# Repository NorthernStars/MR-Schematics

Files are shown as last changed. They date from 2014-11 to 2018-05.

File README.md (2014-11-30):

MR-Schematics
============

This repository includes schematic and pcb layout files for some electronical hardware of the Mixed-Reality system.
Cadsoft Eagle (http://www.cadsoftusa.com/?lang=en) is used to generate the these files. Sometimes also a partlist is included.

Included Files
-----
This repository includes files for the following hardware:
* mrShark - Robot mrShark including programmer and debug/charger boards
* IR Testboard - Board for redirecting serial and IR data for debugging
* IR Transmitter - USB Infrared transmitter
* IR Splitter - Splitter for IR system with high current
* LiPo-Charger MultiBoard - Small Robot LiPo chargers that are connectable to any size of charger station
* LiPo-Charger-Station - 3x3 Robot LiPo charger station with microcontroller

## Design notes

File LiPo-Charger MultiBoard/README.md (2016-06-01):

LiPo-Charger MultiBoard
=======================
This charger consists of several small 50x50mm board that can get connected to each other to build a charger station of your preferred size.
* The charger board includes charging circuits for charging two LiPo batteries with ~200mA/battery.
* The supply board is for connecting the charger boards to a 5V power suplly. Maximum output current ist 5.0A. It's recommended to use max. 10 charger boards at one supply board.

Order online
------------
The pcbs can be ordered very cheap from www.dirtypcbs.com
* Charger: http://dirtypcbs.com/view.php?share=21687&accesskey=b3ce18c981010ed7b3aafff49d6ba531
* Supply: http://dirtypcbs.com/view.php?share=3158&accesskey=d8e7d692d385bc674d54f8e41f2b1a86

The electronic parts should get ordered from Farnell (http://www.farnell.com) and Reichelt (https://secure.reichelt.de/index.html?LANGUAGE=EN).

The LibreOffice calculation Parts-Calculation.ods includes an adjustable list of parts to oder.

Usage
-----
To use the charger, connect at least one charger board to the supply board.
Connect the supply board with your 5V power supply. Attention: There is no protection circuit for higher voltages!
You can connect other chargers to the other sides of any charger already connected to the supply board or to the supply board itself.

I²C / TWI Bus
-------
The charger boards include a I²C (or TWI) interface to connect a microcontroller or any other logic to the robots.
For that the charger board stops the robot (depending on the correct firmware) from booting. After that you can access the robot internal hardware via I²C bus.

There will be an additional board to manage the robots in the future.

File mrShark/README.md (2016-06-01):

mrShark
=======
Here you find schemtics and board layout needed for the Mixed-Relality Robot mrShark.
The main board is the mrShark controlling everything on the robot.
For programming you also need the programmer board. Optional you can use the debuger board to charge the robots batteries and use the serial debug interface to test the robot without infrared communication.

## What you need

* mrShark (main controller board, always use latest version)
* LED-Marker (vision detection marker) 
* mrShark Adapter (programming, debugging and charging)

Also consider using the LiPo-Charger-Multiboard for charging larger sets of robots.

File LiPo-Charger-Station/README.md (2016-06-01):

LiPo-Charger-Station
====================

## DO NOT USE, NOT TESTED AND LAYOUT OUTDATED

This charger station includes LiPo charger circuits to charge 9 robots with 2 LiPo batterys each.
Each battery will be charged with ~500mA. The station includes a microcontroller to access the robots internal hardware.

This project currently not maintained and includes some erros. Use LiPo-Charger MutliBoard instead.

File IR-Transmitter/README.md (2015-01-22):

IR-Transmitter
==============
Use this infrared transmitter to send commands data to the Mixed-Reality robots.
The boeard has a USB connector with and FTDI USB-to-Serial converter so you can plug this board directly into you computer.
The board uses a 115.2kbit/s transmission rate for sending infrared data.

Add a power supply to V+ and GND. You can add any power supply from 5V to 12V (7.5V is recommended).
Add some infrared leds to the LED+ and LED- pads.

You can use the jumper JP1 to use the USB 5V bus power to get a portable IR-Transmitter.
Take care that the maximum output current of the USB bus is 500mA.
If you add ~4 IR-LEDs it should work.

For small mobile IR-Transmitter select a suitable resistor for R2 and don't assemble R3.

Be aware that this board isn't build for high currents!
For that use the IR-Splitter. Maybe you also should use a heatsink on the MOSFET.
To do so, bridge resistor R2 and use 1k ohm resistor for R3. Connect IR data signal for IR-Splitter to LED- and GND of IR-Splitter to GND.

Order
-----
You can order this transmitter via www.dirtypcbs.com
* http://dirtypcbs.com/view.php?share=3876&accesskey=a4be5c8c025c9f4713186b7ca5dc06cf

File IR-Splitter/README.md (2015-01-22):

IR-Splitter
===========
Hardware to split IR data load to seperate MOSFET channels.
Connect external power supply and IR data from IR-Transmitter to the board.
Voltage of power supply depends on you needs but test show that it should be between 5V and 12V (7.5V is recommended).

Connect IR-leds to the 10 IR-OUT pads. Try to balance the number of leds on the channels.
It's highly recommended to use a heatsink on the mosfets.

Test your installation with different intervals of load.
MOSFET's temperature should not be above 80°C!

It is possible to use this pcb as single layer board.

ATTENTION
---------
If you don't use our IR-Transmitter, take care that the IR-Splitter needs an inverted IR data input signal. So HIGH level is LOW and the other way round.

Also be aware that setting IR data input signal to LOW level will cause the leds to light up. This maybe damages them!

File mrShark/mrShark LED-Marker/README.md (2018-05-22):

# mrShark LED-Marker
LEd marker for Mixed-Reality Robotr mrShark.
Includes 3x3 led arry an 4 position lights.
Controlled via I2C/TWI PC9552 led controller.

## PCB Order
Order on 

https://jlcpcb.com/

and upload Gerber File zip.
Dimension of pcb is 26mm x 32mm
    
## Assembly
Place LEDs, ICs and R1, R2, R3 as shown in schematics.
Choose R4 - R11 and R21 corresponding to your LED current (volatge of mrShark is max. 4.1V, average 3.0 - 3.3V, min 2.7V).
Choose R12, R13 for two! LEDs.

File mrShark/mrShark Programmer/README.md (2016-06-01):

# mrShark Programmer
Programming adapter using In-System,-Programming (ISP) over SPI bus of controller.

## DO NOT USE ANYMORE, LAYOUT OUTDATED

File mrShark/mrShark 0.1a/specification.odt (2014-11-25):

mrShark

Platinen-Datenblatt

Platinen-Daten:

Abmaße: | 27x25mm
Bohrungen: | 4x1,5mm (Durchmesser) Vias: 0,24mm
Datenformat: | Eagle (Schaltplan, Platinenlayout) + Datenblatt
Materialdaten: | 35µmCu 1,0mm
Fertigungsdaten: | Lötstopplack (beidseitig) min. Leiterbahnabstand = 6mil (0,150mm)

Bestückung:

Anzahl | Bauteil [Gehäusetyp] | Wert
2 | Kondensator [402] | 18pF
1 | Kondensator [402] | 100nF
2 | Widerstand [0402] | 1kΩ
1 | Buchse 12 Kontakte, RM=0,5mm | Hirose - DF23C-12DS-0.5V(92)
1 | Buchsenleiste 4 Kontakte, RM=2,54mm
2 | Diode [SOT36] | NXP - BAS70-07S
1 | Mikrocontroller [QFN] | Atmel AVR - ATtiny 4313-MU
1 | Motortreiber [10-DFN/MLP] | Allegro Microsystems - A3901SEJTR-T
1 | IRDA-Controller [SOIC] | Microchip - MCP2120-I/SL
1 | IRDA-transciever | Vishay - TFBS4711-TR1
4 | RGB-LED [PLCC6] | Avago Technologies - ASMT-YTD2-0BB02
1 | LED green[0603] | Kingbright - KPT-1608SGC
1 | Quarz 14,7456MHz [CFPX-104] | IQD frequency products - CFPX-104 50/50/10/18 14.7456MHZ
1 | Schalter 2-Polig [DIL] | Multicomp - MCEMR-02-T
2 | Dual NPN Transistor [SOT363] | Rohm - UMX3NTR

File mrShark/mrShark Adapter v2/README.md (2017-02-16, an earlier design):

# mrShark Adapter v2
Additional version of the mrShark Adapter that can be soldered by humans.

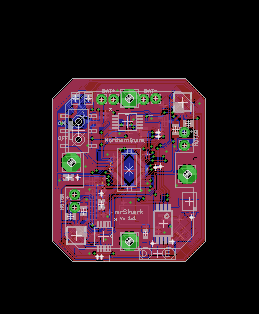
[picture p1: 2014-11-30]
mrShark/mrShark 1.2/board.png

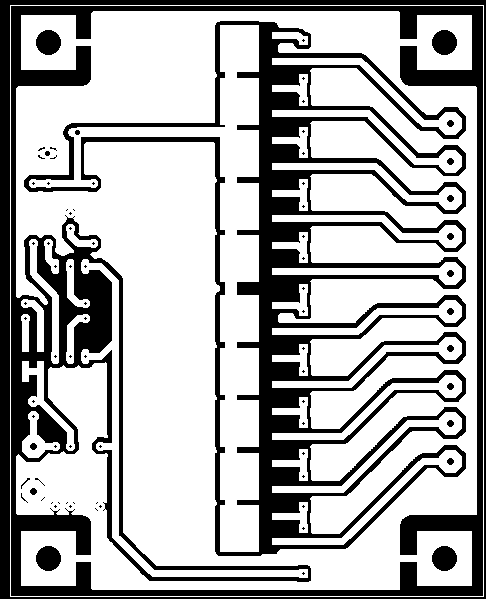
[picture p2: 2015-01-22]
IR-Splitter/layout.png

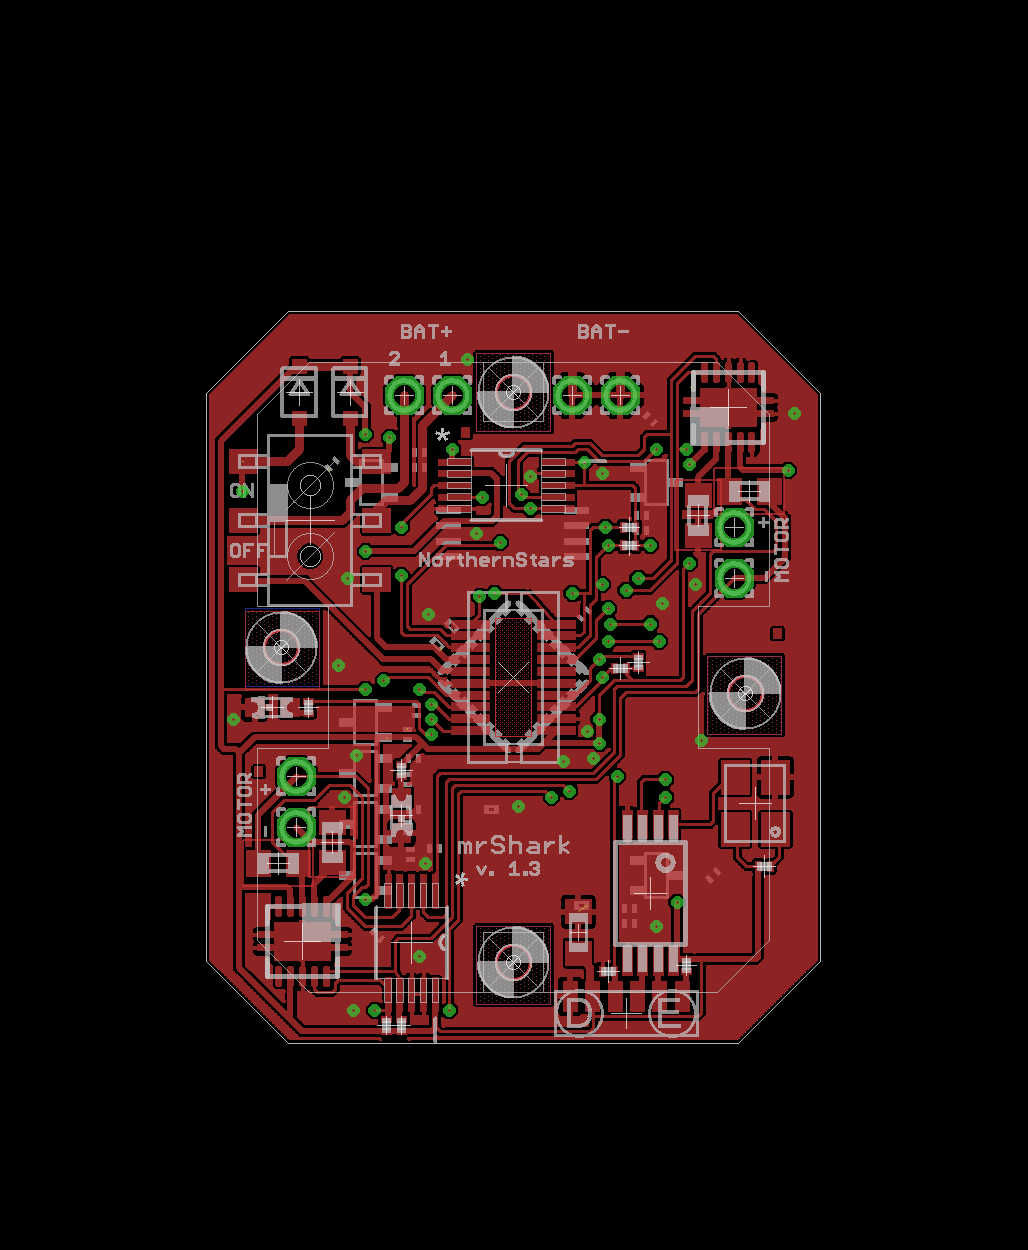
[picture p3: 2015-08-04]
mrShark/mrShark 1.4/TOP-Layer.png

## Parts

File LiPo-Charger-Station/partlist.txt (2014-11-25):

Partname,Value,Package
C1,100n,C0201
C2,100n,C0201
CON_PROG,2X8C7852,7852-2X8
IC1,ATMEGA48/88/168-MU,MLF32
IC2,PCA9306DC,VSSOP8
IC3,TIR1000PWR,PW_R-PDSO-G08
IC4,TFBS4711TR1,TFBS4711
IC5,DRV8830DGQRWSON,S-PDSO-N10
IC6,LTC2990IMSPBF,SOP50P490X110-10N
IC7,DRV8830DGQRWSON,S-PDSO-N10
IC8,LTC2990IMSPBF,SOP50P490X110-10N
LED1,green,CHIPLED_0603
LED2,ASMT-YTD2-0BB02,PLCC6K
LED3,ASMT-YTD2-0BB02,PLCC6K
LED4,ASMT-YTD2-0BB02,PLCC6K
LED5,ASMT-YTD2-0BB02,PLCC6K
LED6,red,CHIPLED_0603
Q1,ASFLM1-1.8432MHZ-L-C-T,HC536
Q2,BC817W,SOT323-BEC
Q3,BC817W,SOT323-BEC
Q4,BC817W,SOT323-BEC
Q5,BC817W,SOT323-BEC
Q6,BC817W,SOT323-BEC
Q7,BC817W,SOT323-BEC
Q8,BC817W,SOT323-BEC
R1,100k,R0201
R2,100k,R0201
R3,100k,R0201
R4,100k,R0201
R5,100k,R0201
R6,130R,R0201
R7,1k8,R0201
R8,1k8,R0201
R9,100k,R0201
R10,27R,R0201
R11,2k,R0201
R12,1k,R0201
R13,2k,R0201
R14,100k,R0201
R15,100k,R0201
R16,100k,R0201
R17,100k,R0201
R18,100k,R0201
R19,560R,R0201
R20,560R,R0201
R21,130R,R0201
R22,130R,R0201
R23,100k,R0201
R24,100k,R0201
R25,560R,R0201
R26,560R,R0201
R27,130R,R0201
R28,130R,R0201
R29,0.95R,R0201
R30,0R2,R0201
R31,0.95R,R0201
R32,0R2,R0201
R33,130R,R0201
R34,1k8,R0201
R35,1k8,R0201
SWITCH_PWR,AYZ0202AGRLC,AYZ0202AGLRC

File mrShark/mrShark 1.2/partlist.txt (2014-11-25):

------------------------------------------------
Eagle partlist from mrshark 11.sch at 24.11.2014 14:29:40
------------------------------------------------

------------------------
PLCC6K
	PLCC6K
		4x	ASMT-YTD2-0BB02
			['LED2', 'LED3', 'LED4', 'LED5']

------------------------
C-EUC0201
	C0201
		2x	18p
			['C3', 'C4']

------------------------
C-EUC0603K
	C0603K
		1x	10µ
			['C5']

------------------------
AYZ0202AGRLC
	AYZ0202AGLRC
		1x	AYZ0202AGRLC
			['SWITCH_PWR']

------------------------
ATMEGA48/88/168-MU
	MLF32
		1x	ATMEGA168-20MU
			['IC1']

------------------------
R-EU_R0201
	R0201
		2x	1k8
			['R34', 'R35']

------------------------
-
	7X-1.8432MBB-T
		1x	TXC
			['Q1']

------------------------
DF12-20DP
	DF12-20DP
		1x	DF12(5.0)-20DP-0.5V
			['CON_PROG']

------------------------
MOUNT-PAD-SQUARE1,5
	0,75-PAD-SQUARE
		4x	MOUNT-PAD-SQUARE1,5
			['H1', 'H2', 'H3', 'H4']

------------------------
R-EU_R0603
	R0603
		1x	0R2
			['R32']

------------------------
BC817W
	SOT323-BEC
		7x	BC817W
			['Q2', 'Q3', 'Q4', 'Q5', 'Q6', 'Q7', 'Q8']

------------------------
DRV8830DGQRWSON
	S-PDSO-N10
		2x	DRV8830DRCT
			['IC5', 'IC7']

------------------------
PCA9540TSSOP8
	TSSOP8
		1x	PCA9540BDP
			['IC2']

------------------------
TXC-7B-SERIESSMD
	TXC_7B_SERIES
		1x	14,7456MHZ
			['Q9']

------------------------
1,6/0,9
	wirepad
		8x	1,6/0,9
			['BAT1+1', 'BAT1-1', 'BAT2+1', 'BAT2-1', 'MOT1', 'MOT2', 'MOT3', 'MOT4']

------------------------
LTC2990IMSPBF
	SOP50P490X110-10N
		2x	LTC2990IMS#PBF
			['IC6', 'IC8']

------------------------
TFBS4711TR1
	TFBS4711
		1x	TFBS4711TR1
			['IC4']

------------------------
PMEG2010EAR
	SOD323-R
		2x	PMEG2010EA
			['D1', 'D2']

------------------------
TIR1000PWR
	PW_R-PDSO-G08
		1x	TIR1000PWR
			['IC3']

------------------------
LEDCHIPLED_0603
	CHIPLED_0603
		1x	red
			['LED6']

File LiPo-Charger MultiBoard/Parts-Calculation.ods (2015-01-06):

LiPo-Charger MultiBoard
Parts calculation
Last Update: | 2014/11/26
No. of Charger Boards: | 20
No. of Supply Boards: | 10
Part | Type | Quantity | # ordered | Farnell Order No. | Price | Total | Toal ordered | Quantity | # ordered | Reichelt Order No. | Price | Total | Total ordered
Pinheader Male | 2.54“ RM, THT | 150 | 150 | 1593428 | 0,054 € | 8,12 € | 8,12 € | 15 | 0 | SL 1X40W 2,54 | 0,300 € | 4,500 € | 0,00 €
Pinheader Female | 2,54“ RM, THT | 150 | 0 | 1804766 | 0,437 € | 65,55 € | 0,00 € | 30 | 30 | BL 1X20W8 2,54 | 0,460 € | 13,800 € | 13,80 €
Resistor 5k6 | SMD 1206 | 50 | 50 | 9236864 | 0,009 € | 0,47 € | 0,47 € | 40 | 0 | SMD 1/4W 5,6K | 0,082 € | 3,280 € | 0,00 €
Resistor 1k8 | SMD 1206 | 100 | 100 | 2139458 | 0,010 € | 1,00 € | 1,00 € | 60 | 0 | SMD 1/4W 1,8K | 0,082 € | 4,920 € | 0,00 €
Resistor 470R | SMD 1206 | 50 | 50 | 9240489 | 0,017 € | 0,85 € | 0,85 € | 50 | 0 | SMD 1/4W 470 | 0,082 € | 4,100 € | 0,00 €
LED red | SMD 1206 | 40 | 40 | 2099245 | 0,078 € | 3,12 € | 3,12 € | 40 | 0 | SMD-LED 1206 RT | 0,110 € | 4,400 € | 0,00 €
LED green | SMD 1206 | 10 | 10 | 2099247 | 0,069 € | 0,69 € | 0,69 € | 10 | 0 | SMD-LED 1206 GN | 0,100 € | 1,000 € | 0,00 €
MCP73832T | SOT-23 | 40 | 40 | 1834891 | 0,363 € | 14,52 € | 14,52 € | 40 | 0 |  |  | 0,000 € | 0,00 €
Header DF12-20DS |  | 20 | 20 | 1324621 | 0,697 € | 13,94 € | 13,94 € | 20 | 0 |  |  | 0,000 € | 0,00 €
Connector Wago 250-202 |  | 10 | 0 | 1891580 | 0,460 € | 4,60 € | 0,00 € | 10 | 10 | WAGO 250-202 | 0,450 € | 4,500 € | 4,50 €
AP1084D33 | TO-252 | 10 | 10 | 1825261 | 0,965 € | 9,65 € | 9,65 € | 10 | 0 |  |  | 0,000 € | 0,00 €
Capacitor 100n | SMD 1206 | 20 | 20 | 2407345 | 0,029 € | 0,58 € | 0,58 € | 20 | 0 | X7R-G1206 100N | 0,050 € | 1,000 € | 0,00 €
Capacitor elko 100µ | SMD d=6,3mm | 10 | 0 | 1973280 | 0,120 € | 1,20 € | 0,00 € | 10 | 10 | SMD ELKO 100/16 | 0,080 € | 0,800 € | 0,80 €
Capacitor elko 220µ | SMD d=6,3mm | 10 | 0 | 2326227 | 0,179 € | 1,79 € | 0,00 € | 10 | 10 | VF 220/6,3 K-D | 0,140 € | 1,400 € | 1,40 €
Parts total = |  | 52,92 € |  |  |  |  |  | 20,50 €
Shipping = |  | 5,95 € |  |  |  |  |  | 5,60 €
TOTAL = |  | 70,06 € |  |  |  |  |  | 26,10 €

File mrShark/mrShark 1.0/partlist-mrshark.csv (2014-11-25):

Quantity | Partname | Value | Package
2 | C1, C2 | 100n | C0201
2 | C3, C4 | 18p | C0201
1 | CON_PROG | DF12(5.0)-20DP-0.5V | DF12-20DP
2 | D1, D2 | PMEG2010EA | SOD323-R
1 | IC1 | ATMEGA168V-10MU | MLF32
1 | IC2 | PCA9540B | TSSOP8
1 | IC3 | TIR1000PWR | PW_R-PDSO-G08
1 | IC4 | TFBS4711TR1 | TFBS4711
2 | IC5, IC7 | DRV8830DRCT | S-PDSO-N10
2 | IC6, IC8 | LTC2990IMS#PBF | SOP50P490X110-10N
1 | LED1 | green | CHIPLED_0603
4 | LED2, LED3, LED4, LED5 | ASMT-YTD2-0BB02 | PLCC6K
1 | LED6 | red | CHIPLED_0603
1 | Q1 | FXO-HC536R-1.8432 | 3.2X2.5
7 | Q2, Q3, Q4, Q5, Q6, Q7, Q8 | BC817W | SOT323-BEC
1 | Q9 | 11.0592MHZ | TXC_7B_SERIES
12 | R1, R2, R4, R5, R9, R14, R15, R16, R17, R18, R23, R24 | 100k | R0201
6 | R6, R21, R22, R27, R28, R33 | 130R | R0201
4 | R7, R8, R34, R35 | 1k8 | R0201
1 | R10 | 27R | R0201
2 | R11, R13 | 2k | R0201
1 | R12 | 1k | R0201
4 | R19, R20, R25, R26 | 560R | R0201
2 | R29, R31 | 0.95R | R0603
2 | R30, R32 | 0R2 | R0603
1 | SWITCH_PWR | AYZ0202AGRLC | AYZ0202AGLRC

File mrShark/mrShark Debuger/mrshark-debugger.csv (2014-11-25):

Quantity | Partname | Value | Package
1 | C1 | 100n | C0201
2 | C2, C6 | 4.7uF | C0805
1 | CON | DF12-20DS | DF12-20DS
2 | D1, D2 | RED | CHIP-LED0603
1 | IC1 | LM317MBSTT3 | SOT223
1 | IC2 | FT232RQ | QFN32
2 | IC3, IC4 | MCP73831T-2ATI/OT | SOT23-5
1 | R1 | 165k | R0201
1 | R2 | 100k | R0201
2 | R3, R9 | 130R | R0201
2 | R4, R15 | 2K2 | R0201

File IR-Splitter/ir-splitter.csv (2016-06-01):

Qty | Value | Device | Package | Parts | Description
10 |  | 3,81/1,4 | 3,81/1,4 | IR-OUT1, IR-OUT2, IR-OUT3, IR-OUT4, IR-OUT5, IR-OUT6, IR-OUT7, IR-OUT8, IR-OUT9, IR-OUT10 | THROUGH-HOLE PAD
1 |  | LEDCHIPLED_1206 | CHIPLED_1206 | LED1 | LED
3 | 1k | R-EU_R1206 | R1206 | R1, R2, R3 | RESISTOR, European symbol
1 | 250-202 | 250-202 | P-250-202 | SUPPLY | Serie 250, 1-Leiter-Klemmenleiste für Leiterplatten 1 Lötstift/Pol versetzt / Series 250, 1-conductor PCB terminal strip 1 solder pin/pole, staggeredPolzahl / Pole No.: 2 Rastermaß / Pitch: 3.5 mmBemessungsspannung / Rated Voltage: 320 VNennstrom / Nominal Current: 8 ALeiterquerschnitt / Conductor Size: 0.2 - 1.5 mm²Anschlusstechnik / Connection Technology: Steckklemm-Anschluss Lötstiftlänge: / Solder Pin Length: 3.6 mmLeitereinführung (zur Platine) / Conductor entry angle (to PCB): 45 °Farbe / Color: grau / gray Stand: 01.01.2012. Die jeweils aktuellen Daten zu diesem Artikel finden Sie in unserem Produktkatalog, den Sie unter www.wago.com einsehen können. As of: 01/01/2012. Please find the newest data for this article in our product catalogue, which can be viewed under www.wago.com.
1 | 330R | R-EU_R1206 | R1206 | R6 | RESISTOR, European symbol
10 | >100k | R-EU_R1206 | R1206 | R4, R5, R7, R8, R9, R10, R11, R12, R13, R14 | RESISTOR, European symbol
2 | BC548B | BC548B | TO92-EBC | Q1, Q2 | NPN Transistor
1 | IR-IN-DATA | 3,81/1,4 | 3,81/1,4 | IR_DATA | THROUGH-HOLE PAD
1 | IR-IN-GND | 3,81/1,4 | 3,81/1,4 | GND | THROUGH-HOLE PAD
10 | IRFR024N | IRLR3915PBF | D-PAK | T1, T2, T3, T4, T5, T6, T7, T8, T9, T10
4 | MOUNT-PAD-SQUARE4.5 | MOUNT-PAD-SQUARE4.5 | 4,5-PAD-SQUARE | H1, H2, H3, H4 | MOUNTING PAD, square

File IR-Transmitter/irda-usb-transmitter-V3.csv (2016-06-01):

Qty | Value | Device | Package | Parts | Description
1 |  | PINHD-2X2 | 2X02 | JP1 | PIN HEADER
2 |  | R-EU_R1206 | R1206 | R2, R3 | RESISTOR, European symbol
2 |  | SMD5 | SMD2,54-5,08 | GND, V+ | SMD PAD
1 |  | USB-B-S | USB-B-SMT | USB | USB Connectors
1 | 100K | R-EU_R1206 | R1206 | R1 | RESISTOR, European symbol
2 | 100n | C-EUC1206 | C1206 | C3, C7 | CAPACITOR, European symbol
1 | 220µ | CPOL-EUE3.5-8 | E3,5-8 | C6 | POLARIZED CAPACITOR, European symbol
2 | 22p | C-EUC0805 | C0805 | C1, C2 | CAPACITOR, European symbol
1 | 7.3728MHz | CRYTALHC49UP | HC49UP | Q2 | CRYSTAL
1 | FT232RL | FT232RL | SSOP28DB | IC1 | USB UART
2 | IR-LED | WIREPADSMD5-2,5 | 5-2,5 | LED+, LED- | Wire PAD connect wire on PCB
1 | IRLR3915PBF | IRLR3915PBF | D-PAK | U$1
1 | MCP2120 | MCP2120 | SO-14 | IC2
4 | MOUNT-HOLE2.8 | MOUNT-HOLE2.8 | 2,8 | H1, H2, H3, H4 | MOUNTING HOLE with drill center marker

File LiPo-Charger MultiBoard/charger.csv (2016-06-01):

Qty | Value | Device | Package | Parts | Description
4 |  | PINHD-1X02_2.54-90° | 1X02/90 | FEMALE_B, FEMALE_R, MALE_L, MALE_T | PIN HEADER
8 |  | PINHD-1X04_2.54-90° | 1X04/90 | FEMALE_BL, FEMALE_BR, FEMALE_RB, FEMALE_RT, MALE_LB, MALE_LT, MALE_TL, MALE_TR | PIN HEADER
2 | 1k8 | R-EU_R1206 | R1206 | R5, R6 | RESISTOR, European symbol
2 | 4.7µ, 5V | C-EUC1206 | C1206 | C1, C2 | CAPACITOR, European symbol
2 | 470R | R-EU_R1206 | R1206 | R1, R3 | RESISTOR, European symbol
2 | 5k6 | R-EU_R1206 | R1206 | R2, R4 | RESISTOR, European symbol
1 | DF12-20DS | DF12-20DS | DF12-20DS | BOT_CON | HRS-Hirose DF12-Series
2 | MCP73832T | MCP73832T-2DCI/OT | SOT95P300X145-5N | IC1, IC2 | IC, BATT CHARGER, Li-Ion Li-Polymer, 500 mA
2 | red | LEDCHIPLED_1206 | CHIPLED_1206 | LED1, LED2 | LED

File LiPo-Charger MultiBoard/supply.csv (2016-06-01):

Qty | Value | Device | Package | Parts | Description
4 |  | PINHD-1X02_2.54-90° | 1X02/90 | FEMALE_B, FEMALE_R, MALE_L, MALE_T | PIN HEADER
8 |  | PINHD-1X04_2.54-90° | 1X04/90 | FEMALE_BL, FEMALE_BR, FEMALE_RB, FEMALE_RT, MALE_LB, MALE_LT, MALE_TL, MALE_TR | PIN HEADER
2 | 100n | C-EUC1206 | C1206 | C1, C2 | CAPACITOR, European symbol
1 | 100µ | CPOL-EUUD-6,3X8,8 | UD-6,3X5,8_NICHICON | C3 | POLARIZED CAPACITOR, European symbol
2 | 1k8 | R-EU_R1206 | R1206 | R2, R3 | RESISTOR, European symbol
1 | 220µ | CPOL-EUUD-6,3X7,7 | UD-6,3X7,7_NICHICON | C4 | POLARIZED CAPACITOR, European symbol
1 | 250-202 | 250-202 | P-250-202 | SUPPLY | Serie 250, 1-Leiter-Klemmenleiste für Leiterplatten 1 Lötstift/Pol versetzt / Series 250, 1-conductor PCB terminal strip 1 solder pin/pole, staggeredPolzahl / Pole No.: 2 Rastermaß / Pitch: 3.5 mmBemessungsspannung / Rated Voltage: 320 VNennstrom / Nominal Current: 8 ALeiterquerschnitt / Conductor Size: 0.2 - 1.5 mm²Anschlusstechnik / Connection Technology: Steckklemm-Anschluss Lötstiftlänge: / Solder Pin Length: 3.6 mmLeitereinführung (zur Platine) / Conductor entry angle (to PCB): 45 °Farbe / Color: grau / gray Stand: 01.01.2012. Die jeweils aktuellen Daten zu diesem Artikel finden Sie in unserem Produktkatalog, den Sie unter www.wago.com einsehen können. As of: 01/01/2012. Please find the newest data for this article in our product catalogue, which can be viewed under www.wago.com.
1 | 470R | R-EU_R1206 | R1206 | R1 | RESISTOR, European symbol
1 | AP1084D33 | AP1084 | TO252 | IC1 | AP1084
1 | green | LEDCHIPLED_1206 | CHIPLED_1206 | LED1 | LED

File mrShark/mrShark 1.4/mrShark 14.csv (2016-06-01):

Qty | Value | Device | Package | Parts | Description
8 |  | 1,6/0,9 | 1,6/0,9 | BAT1+1, BAT1-1, BAT2+1, BAT2-1, MOT1, MOT2, MOT3, MOT4 | THROUGH-HOLE PAD
2 | 0.91R | R-EU_R0603 | R0603 | R29, R31 | RESISTOR, European symbol
2 | 0R2 | R-EU_R0603 | R0603 | R30, R32 | RESISTOR, European symbol
12 | 100k | R-EU_R0201 | R0201 | R1, R2, R4, R5, R9, R14, R15, R16, R17, R18, R23, R24 | RESISTOR, European symbol
2 | 100n | C-EUC0201 | C0201 | C1, C2 | CAPACITOR, European symbol
1 | 10µ | C-EUC0603K | C0603K | C5 | CAPACITOR, European symbol
4 | 130R | R-EU_R0201 | R0201 | R21, R22, R27, R28 | RESISTOR, European symbol
1 | 14,7456MHZ | TXC-7B-SERIESSMD | TXC_7B_SERIES | Q9 | TXC 7B SERIES
2 | 18p | C-EUC0201 | C0201 | C3, C4 | CAPACITOR, European symbol
1 | 1k | R-EU_R0201 | R0201 | R12 | RESISTOR, European symbol
4 | 1k8 | R-EU_R0201 | R0201 | R7, R8, R34, R35 | RESISTOR, European symbol
1 | 200R | R-EU_R0201 | R0201 | R33 | RESISTOR, European symbol
1 | 27R | R-EU_R0201 | R0201 | R10 | RESISTOR, European symbol
2 | 2k | R-EU_R0201 | R0201 | R11, R13 | RESISTOR, European symbol
4 | 560R | R-EU_R0201 | R0201 | R19, R20, R25, R26 | RESISTOR, European symbol
1 | 87R | R-EU_R0201 | R0201 | R6 | RESISTOR, European symbol
4 | ASMT-YTD2-0BB02 | PLCC6K | PLCC6K | LED2, LED3, LED4, LED5 | Standart PLCC6 Package RGB LED
1 | ATMEGA168-20MU | ATMEGA48/88/168-MU | MLF32 | IC1
1 | AYZ0202AGRLC | AYZ0202AGRLC | AYZ0202AGLRC | SWITCH_PWR | AYZ Switch Series
7 | BC817W | BC817W | SOT323-BEC | Q2, Q3, Q4, Q5, Q6, Q7, Q8 | NPN Transistor
1 | DF12(5.0)-20DP-0.5V | DF12-20DP | DF12-20DP | CON_PROG | HRS-Hirose DF12-Series
2 | DRV8830DRCT | DRV8830DGQRWSON | S-PDSO-N10 | IC5, IC7 | LOW-VOLTAGE MOTOR DRIVER WITH SERIAL INTERFACE
2 | LTC2990IMS#PBF | LTC2990IMSPBF | SOP50P490X110-10N | IC6, IC8 | Quad I2C Voltage, Current and Temperature Monitor
4 | MOUNT-HOLE1,5 | MOUNT-HOLE1,5 | 1,5 | H1, H2, H3, H4 | MOUNTING HOLE with drill center marker
1 | PCA9540BDP | PCA9540TSSOP8 | TSSOP8 | IC2 | PCA9540
2 | PMEG2010EA | PMEG2010EAR | SOD323-R | D1, D2 | NXP - Low V F (MEGA) Schottky barrier diode
1 | TFBS4711TR1 | TFBS4711TR1 | TFBS4711 | IC4 | TRANSCEIVER IRDA
1 | TIR1000PWR | TIR1000PWR | PW_R-PDSO-G08 | IC3 | Texas Instruments TIR1000
1 | TXC - 7X-1.8432MBB-T - OSC, 1.8432MHZ | 7X-SERIES | 3.2X2.5 | Q1 | TXC 7X SERIES
1 | green | LEDCHIPLED_0603 | CHIPLED_0603 | LED1 | LED
1 | red | LEDCHIPLED_0603 | CHIPLED_0603 | LED6 | LED

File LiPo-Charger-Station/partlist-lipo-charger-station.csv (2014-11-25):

Quantity | Partname | Value | Package
1 | C1 | 10µ | PANASONIC_D
1 | C2 | 22µ | PANASONIC_E
1 | C3 | 100n | C0201
2 | C4, C5 | 100µ | PANASONIC_G
50 | C6, C7, C8, C9, C10, C11, C12, C13, C14, C15, C16, C17, C18, C19, C20, C21, C22, C23, C24, C25, C26, C27, C28, C29, C30, C31, C32, C33, C34, C35, C36, C37, C38, C39, C40, C41, C42, C43, C44, C45, C46, C47, C48, C49, C50, C51, C52, C53, C54, C55 | 4.7uF | C0201
25 | CON_PROG, CON_PROG1, CON_PROG2, CON_PROG3, CON_PROG4, CON_PROG5, CON_PROG6, CON_PROG7, CON_PROG8, CON_PROG9, CON_PROG10, CON_PROG11, CON_PROG12, CON_PROG13, CON_PROG14, CON_PROG15, CON_PROG16, CON_PROG17, CON_PROG18, CON_PROG19, CON_PROG20, CON_PROG21, CON_PROG22, CON_PROG23, CON_PROG24 | 2X8MALE | 7078-2X8
50 | D1, D2, D3, D4, D5, D6, D7, D8, D9, D10, D11, D12, D13, D14, D15, D16, D17, D18, D19, D20, D21, D22, D23, D24, D25, D26, D27, D28, D29, D30, D31, D32, D33, D34, D35, D36, D37, D38, D39, D40, D41, D42, D43, D44, D45, D46, D47, D48, D49, D50 | RED | CHIP-LED0603
1 | IC1 | LT1083CP-5 | TO3P
1 | IC2 | ATMEGA8A-AU | TQFP32-08
1 | IC3 | AP1084D33G-13 | TO252
1 | ISP | TSM-105-04-T-DV | 2X05SMD
1 | LCD | TSM-116-04-T-SV | 1X16SMD
5 | R1, R4, R5, R6, R7 | 100k | R0201
12 | R2, R3, R109, R110, R111, R112, R113, R114, R115, R116, R117, R118 | 1k8 | R0201
1 | R8 | 5R3 | R0201
50 | R9, R10, R11, R12, R13, R14, R21, R22, R23, R24, R25, R26, R33, R34, R35, R36, R37, R38, R45, R46, R47, R48, R49, R50, R57, R58, R59, R60, R61, R62, R69, R70, R71, R72, R73, R74, R81, R82, R83, R84, R85, R86, R93, R94, R95, R96, R97, R98, R105, R106 | 130R | R0201
50 | R15, R16, R17, R18, R19, R20, R27, R28, R29, R30, R31, R32, R39, R40, R41, R42, R43, R44, R51, R52, R53, R54, R55, R56, R63, R64, R65, R66, R67, R68, R75, R76, R77, R78, R79, R80, R87, R88, R89, R90, R91, R92, R99, R100, R101, R102, R103, R104, R107, R108 | 2K | R0201
1 | SUPPLY | 250-202 | P-250-202
4 | T1, T2, T3, T4 | EVQQ2F03W | SMD_TASTER_PANASONIC
50 | U1, U2, U3, U4, U5, U6, U7, U8, U9, U10, U11, U12, U13, U14, U15, U16, U17, U18, U19, U20, U21, U22, U23, U24, U25, U26, U27, U28, U29, U30, U31, U32, U33, U34, U35, U36, U37, U38, U39, U40, U41, U42, U43, U44, U45, U46, U47, U48, U49, U50 | MCP73831T-2ATI/OT | SOT23-5

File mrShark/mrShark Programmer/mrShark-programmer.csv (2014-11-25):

Quantity | Partname | Value | Package
1 | C1 | 100n | C0201
1 | CON | DF12-20DS | DF12-20DS
1 | IC1 | LM317MBSTT3 | SOT223
1 | ISP1 | TSM-105-04-T-DV | 2X05SMD
1 | ISP2 | TSM-103-04-T-DV | 2X03SMD
1 | R1 | 165k | R0201
1 | R2 | 100k | R0201

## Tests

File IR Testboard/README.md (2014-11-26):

IR-Testboard
============
Board to redirect IR data or/and serial Data.
Use jumpers on the board to redircet the RX or TX data to PC or an external logic.

Used for testing IR reciever.

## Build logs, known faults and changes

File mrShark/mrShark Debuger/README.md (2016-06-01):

# mrShark Debugger
Debugging adapter using FT232 FTDI chip to translate controlers debugging uart to usb.

## DO NOT USE ANYMORE, LAYOUT OUTDATED

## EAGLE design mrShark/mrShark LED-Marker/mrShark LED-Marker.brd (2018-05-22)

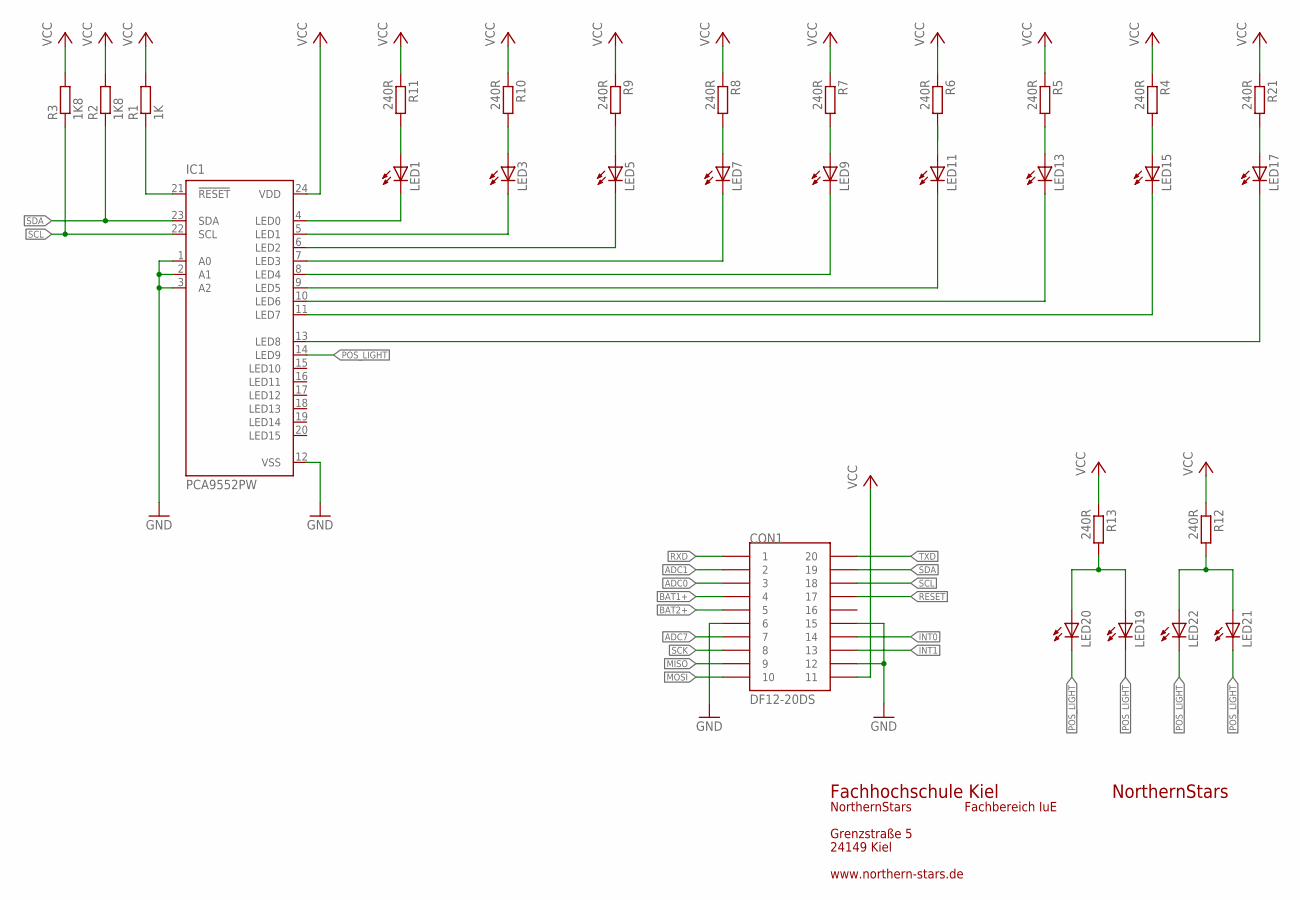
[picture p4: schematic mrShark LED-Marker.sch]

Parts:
CON1: DF12-20DS
IC1: PCA9552PW; TSSOP24
LED1, LED3, LED5, LED7, LED9, LED11, LED13, LED15, LED17, LED19, LED20, LED21, LED22: LEDCHIPLED_0603; CHIPLED_0603
R1: 1K; R0603
R2, R3: 1K8; R0603
R4, R5, R6, R7, R8, R9, R10, R11, R12, R13, R21: 240R; R0603

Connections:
ADC0: CON1.3
ADC1: CON1.2
ADC7: CON1.7
BAT1+: CON1.4
BAT2+: CON1.5
GND: CON1.6, CON1.12, CON1.15, IC1.1 (A0), IC1.2 (A1), IC1.3 (A2), IC1.12 (VSS)
INT0: CON1.14
INT1: CON1.13
MISO: CON1.9
MOSI: CON1.10
unnamed: IC1.21 (!RESET), R1.1
unnamed: LED17.A, R21.2
unnamed: LED21.A, LED22.A, R12.2
unnamed: LED15.A, R4.2
unnamed: LED13.A, R5.2
unnamed: LED11.A, R6.2
unnamed: LED9.A, R7.2
unnamed: LED7.A, R8.2
unnamed: LED19.A, LED20.A, R13.2
unnamed: LED5.A, R9.2
unnamed: LED3.A, R10.2
unnamed: LED1.A, R11.2
unnamed: IC1.4 (LED0), LED1.C
unnamed: IC1.5 (LED1), LED3.C
unnamed: IC1.6 (LED2), LED5.C
unnamed: IC1.7 (LED3), LED7.C
unnamed: IC1.8 (LED4), LED9.C
unnamed: IC1.9 (LED5), LED11.C
unnamed: IC1.10 (LED6), LED13.C
unnamed: IC1.11 (LED7), LED15.C
unnamed: IC1.13 (LED8), LED17.C
POS_LIGHT: IC1.14 (LED9), LED19.C, LED20.C, LED21.C, LED22.C
RESET: CON1.17
RXD: CON1.1
SCK: CON1.8
SCL: CON1.18, IC1.22 (SCL), R3.1
SDA: CON1.19, IC1.23 (SDA), R2.1
TXD: CON1.20
VCC: CON1.11, IC1.24 (VDD), R1.2, R2.2, R3.2, R4.1, R5.1, R6.1, R7.1, R8.1, R9.1, R10.1, R11.1, R12.1, R13.1, R21.1

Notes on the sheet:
NorthernStars
Fachhochschule Kiel
Grenzstraße 5
24149 Kiel
Fachbereich IuE
www.northern-stars.de

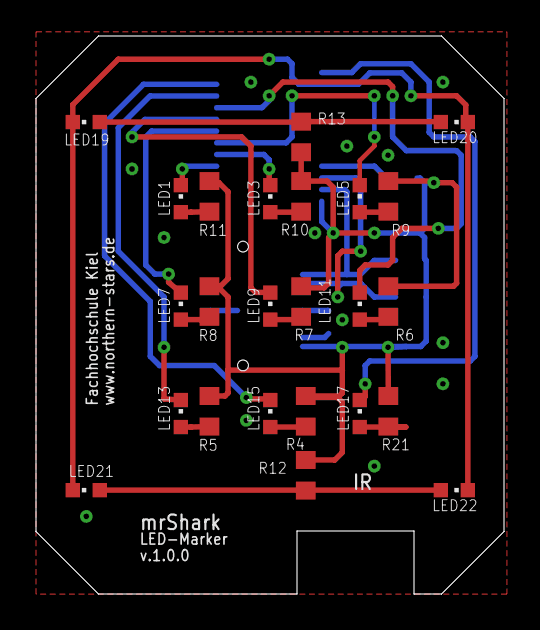
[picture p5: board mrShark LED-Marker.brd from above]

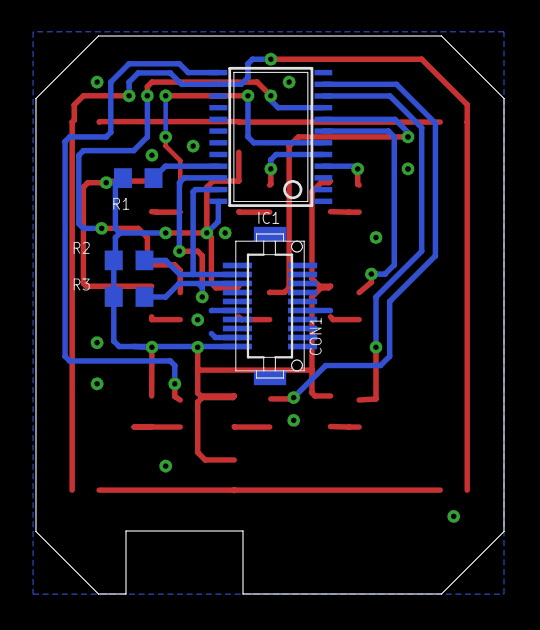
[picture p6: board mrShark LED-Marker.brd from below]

Board: 2 copper layers, 26.0 x 31.0 mm, 29 parts (5 on the bottom side), 26 nets.

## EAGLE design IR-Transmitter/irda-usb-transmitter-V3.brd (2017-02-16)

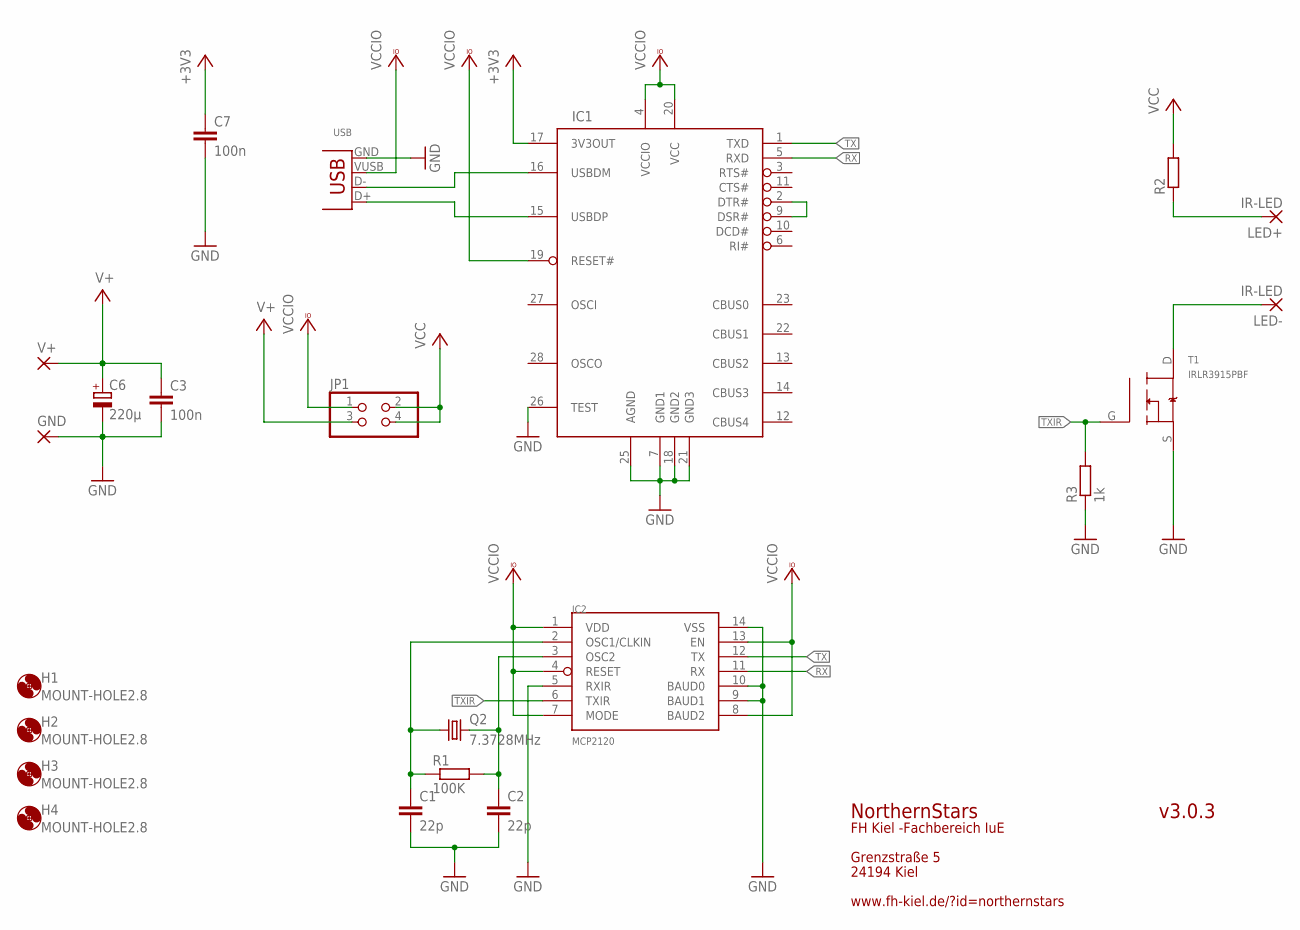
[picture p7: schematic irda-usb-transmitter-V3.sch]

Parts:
C1, C2: 22p; C0805
C3, C7: 100n; C1206
C6: 220µ; E3,5-8
GND: SMD5; SMD2,54-5,08
H1, H2, H3, H4: MOUNT-HOLE2.8; 2,8
IC1: FT232RL; SSOP28DB
IC2: MCP2120; SO-14
JP1: PINHD-2X2; 2X02
LED+: IR-LED; 5-2,5
LED-: IR-LED; 5-2,5
Q2: 7.3728MHz; HC49UP
R1: 100K; R1206
R2: R-EU_R1206; R1206
R3: 1k; R1206
T1: IRLR3915PBF; D-PAK
USB: USB-B-S; USB-B-SMT
V+: SMD5; SMD2,54-5,08

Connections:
+3V3: C7.1, IC1.17 (3V3OUT)
D+: IC1.15 (USBDP), USB.D+
D-: IC1.16 (USBDM), USB.D-
GND: C1.2, C2.2, C3.2, C6.-, C7.2, GND.1, IC1.7 (GND1), IC1.18 (GND2), IC1.21 (GND3), IC1.25 (AGND), IC1.26 (TEST), IC2.5 (RXIR), IC2.9 (BAUD1), IC2.10 (BAUD0), IC2.14 (VSS), R3.1, T1.S, USB.GND
IRLEDS-: LED-.1, T1.D
unnamed: LED+.1, R2.1
unnamed: IC1.2 (DTR#), IC1.9 (DSR#)
unnamed: C1.1, IC2.2 (OSC1/CLKIN), Q2.1, R1.1
unnamed: C2.1, IC2.3 (OSC2), Q2.2, R1.2
RX: IC1.5 (RXD), IC2.11 (RX)
TX: IC1.1 (TXD), IC2.12 (TX)
TXIR: IC2.6 (TXIR), R3.2, T1.G
V+: C3.1, C6.+, JP1.3, V+.1
VCC: JP1.2, JP1.4, R2.2
VCCIO: IC1.4 (VCCIO), IC1.19 (RESET#), IC1.20 (VCC), IC2.1 (VDD), IC2.4 (RESET), IC2.7 (MODE), IC2.8 (BAUD2), IC2.13 (EN), JP1.1, USB.VUSB (VBUS)

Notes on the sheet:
v3.0.3
NorthernStars
FH Kiel -Fachbereich IuE
Grenzstraße 5
24194 Kiel
www.fh-kiel.de/?id=northernstars

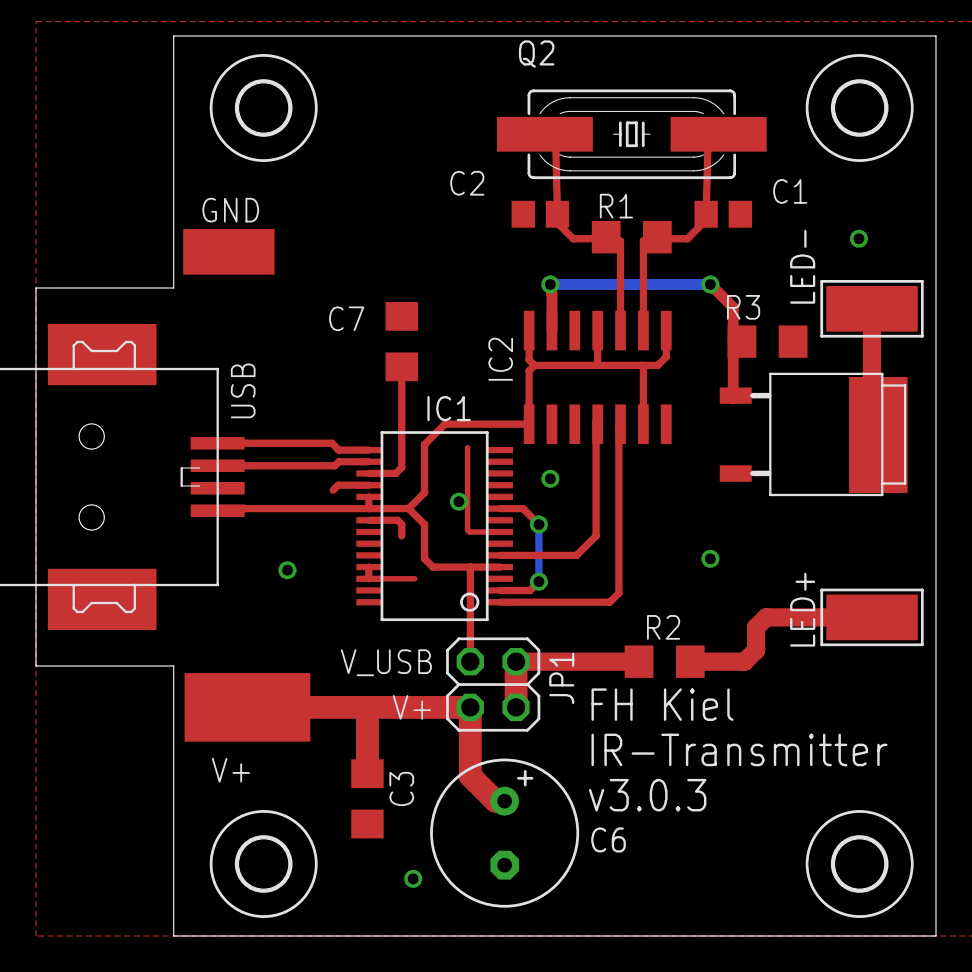
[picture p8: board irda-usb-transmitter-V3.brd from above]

Board: 2 copper layers, 50.0 x 50.0 mm, 22 parts (0 on the bottom side), 15 nets.

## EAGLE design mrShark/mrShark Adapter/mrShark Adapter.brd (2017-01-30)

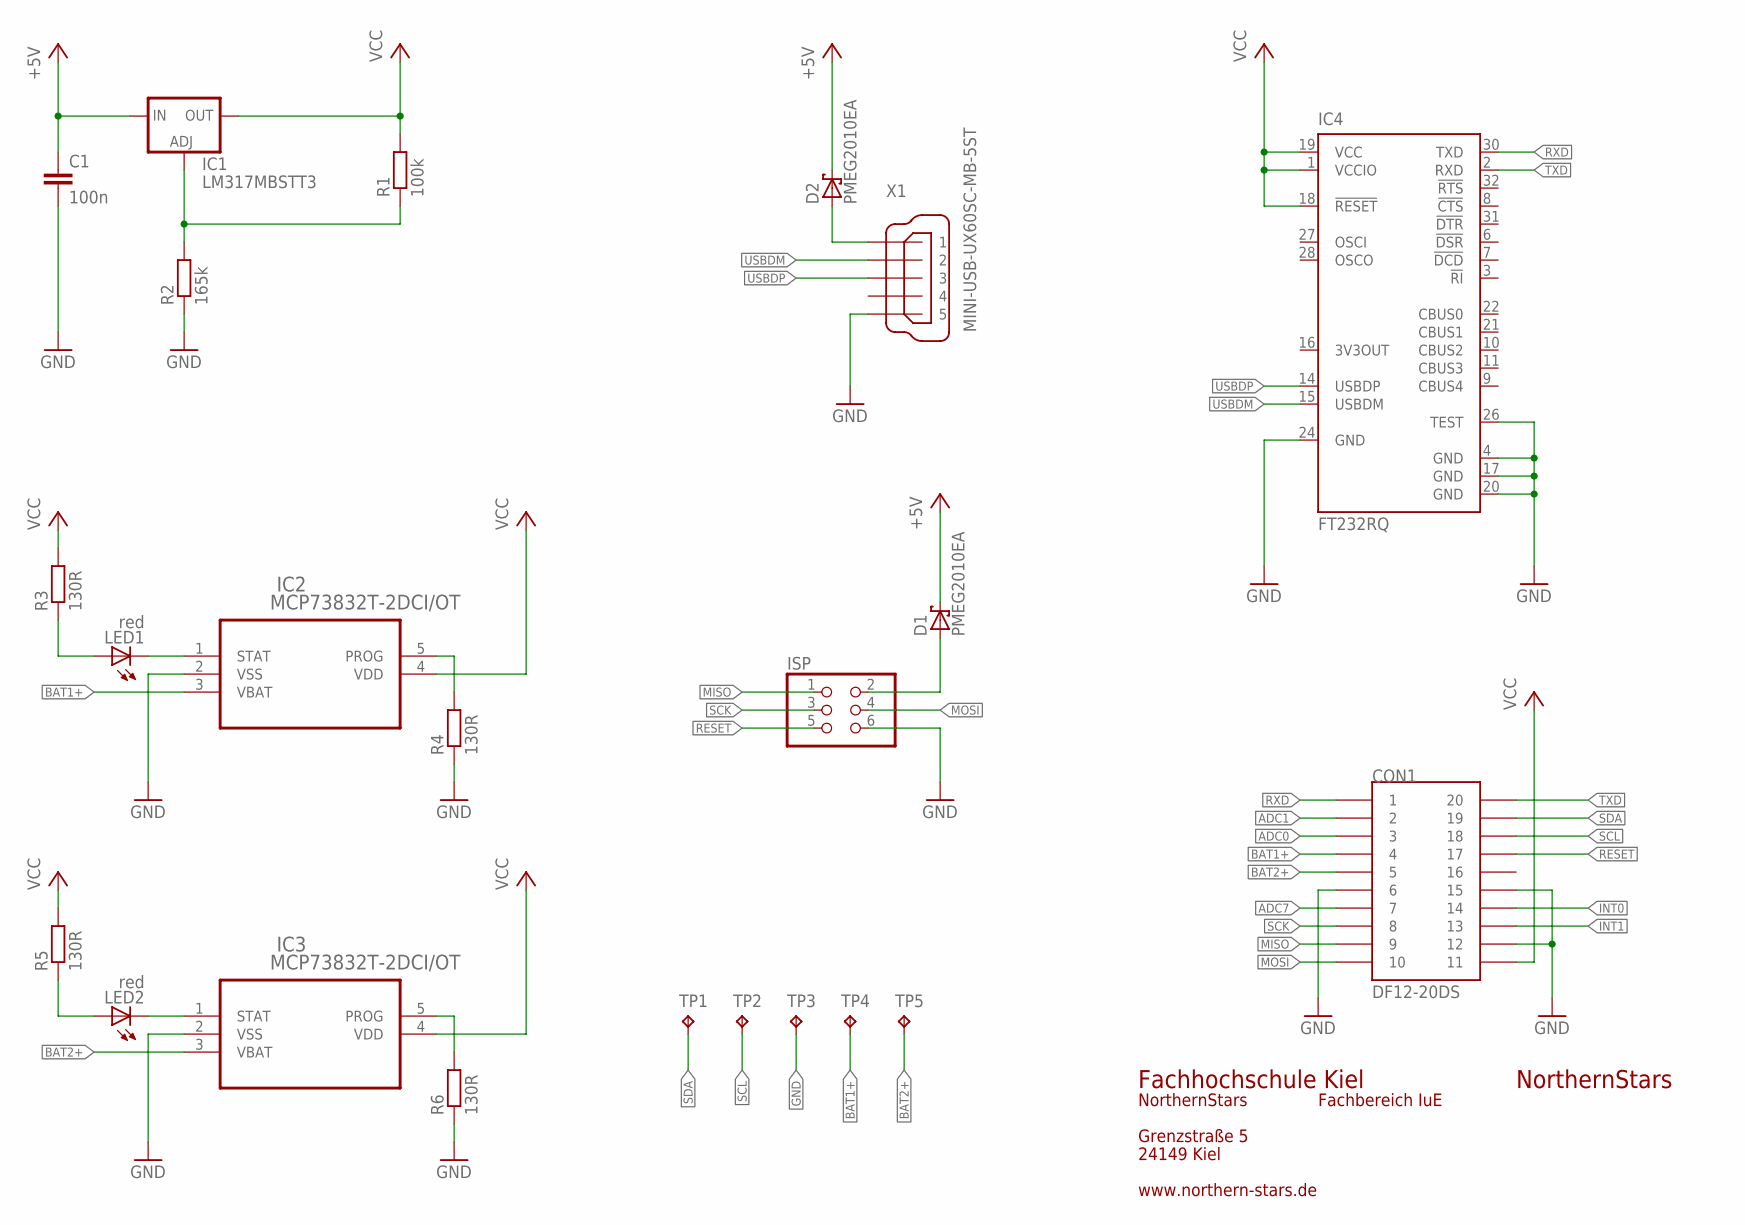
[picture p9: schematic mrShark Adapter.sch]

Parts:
C1: 100n; C0603
CON1: DF12-20DS
D1, D2: PMEG2010EA; SOD323-R
IC1: LM317MBSTT3; SOT223
IC2, IC3: MCP73832T-2DCI/OT; SOT95P300X145-5N
IC4: FT232RQ; QFN32
ISP: PINHD-2X03_2.54-SMD; 2X03SMD
LED1, LED2: red; CHIP-LED0603
R1: 100k; R0603
R2: 165k; R0603
R3, R4, R5, R6: 130R; R0603
TP1, TP2, TP3, TP4, TP5: TPTP06SQ; TP06SQ
X1: MINI-USB-UX60SC-MB-5ST; UX60SC-MB-5ST

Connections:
+5V: C1.1, D1.C, D2.C, IC1.3 (IN)
ADC0: CON1.3
ADC1: CON1.2
ADC7: CON1.7
BAT1+: CON1.4, IC2.3 (VBAT), TP4.TP
BAT2+: CON1.5, IC3.3 (VBAT), TP5.TP
GND: C1.2, CON1.6, CON1.12, CON1.15, IC2.2 (VSS), IC3.2 (VSS), IC4.4 (GND), IC4.17 (GND), IC4.20 (GND), IC4.24 (GND), IC4.26 (TEST), ISP.6, R2.1, R4.1, R6.1, TP3.TP, X1.5
INT0: CON1.14
INT1: CON1.13
MISO: CON1.9, ISP.1
MOSI: CON1.10, ISP.4
unnamed: IC1.1 (ADJ), R1.1, R2.2
unnamed: IC2.1 (STAT), LED1.C
unnamed: LED1.A, R3.1
unnamed: D1.A, ISP.2
unnamed: IC2.5 (PROG), R4.2
unnamed: LED2.A, R5.1
unnamed: IC3.1 (STAT), LED2.C
unnamed: IC3.5 (PROG), R6.2
unnamed: D2.A, X1.1
RESET: CON1.17, ISP.5
RXD: CON1.1, IC4.30 (TXD)
SCK: CON1.8, ISP.3
SCL: CON1.18, TP2.TP
SDA: CON1.19, TP1.TP
TXD: CON1.20, IC4.2 (RXD)
USBDM: IC4.15 (USBDM), X1.2
USBDP: IC4.14 (USBDP), X1.3
VCC: CON1.11, IC1.4 (OUT), IC2.4 (VDD), IC3.4 (VDD), IC4.1 (VCCIO), IC4.18 (!RESET), IC4.19 (VCC), R1.2, R3.2, R5.2

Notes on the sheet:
NorthernStars
Fachhochschule Kiel
Grenzstraße 5
24149 Kiel
Fachbereich IuE
www.northern-stars.de

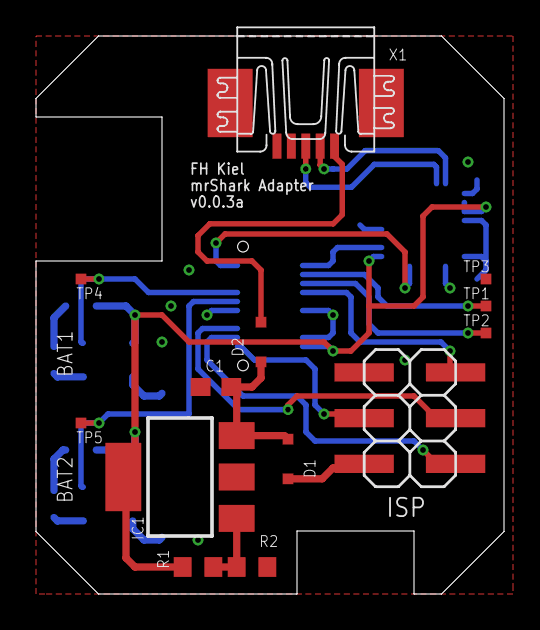
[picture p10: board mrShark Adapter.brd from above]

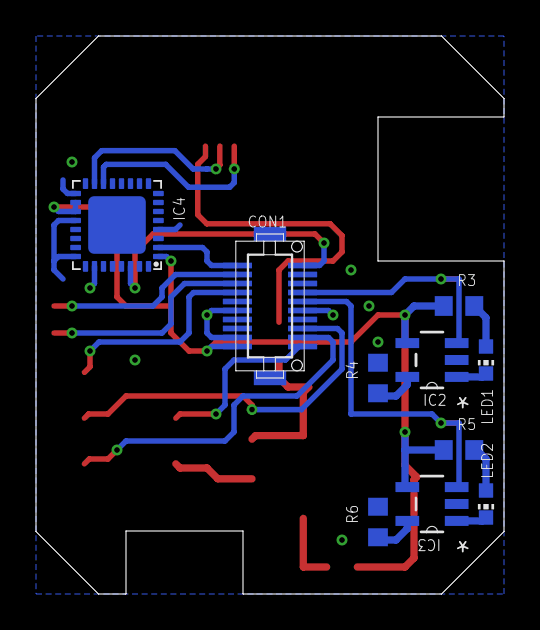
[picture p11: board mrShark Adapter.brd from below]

Board: 2 copper layers, 26.0 x 31.0 mm, 23 parts (10 on the bottom side), 24 nets.

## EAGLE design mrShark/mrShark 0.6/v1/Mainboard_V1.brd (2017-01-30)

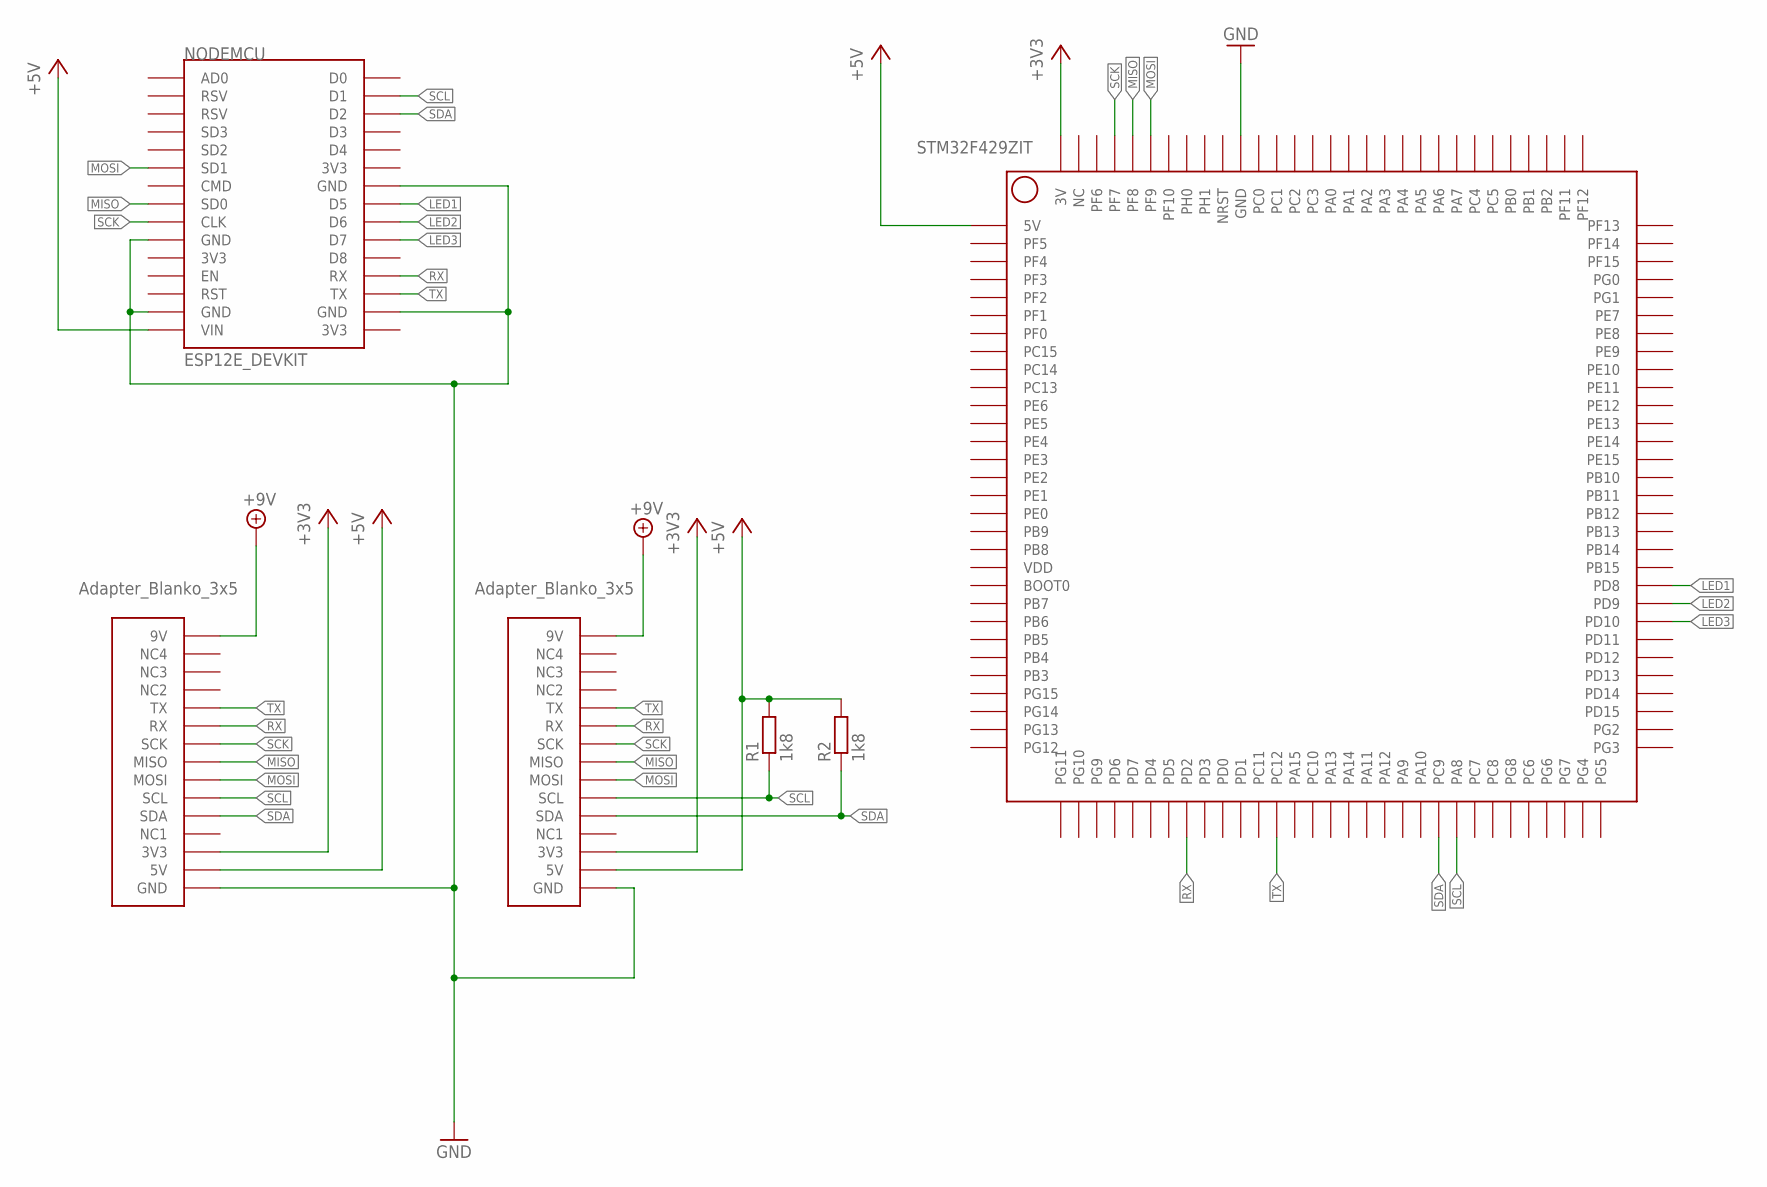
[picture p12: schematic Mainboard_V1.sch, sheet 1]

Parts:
NODEMCU: ESP12E_DEVKIT
R1, R2: 1k8; R0805
U$1: STM32F429ZIT
U$2, U$3: ADAPTER_BLANKO_3X5B1; ADAPTER_BLANKO_3X5_B1

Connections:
+3V3: U$1.3V, U$1.3V1 (3V), U$2.3V3, U$2.3V3_1 (3V3), U$3.3V3, U$3.3V3_1 (3V3); also elsewhere on the board
+5V: NODEMCU.VIN, R1.2, R2.2, U$1.5V, U$1.5V1 (5V), U$2.5V, U$2.5V_1 (5V), U$3.5V, U$3.5V_1 (5V); also elsewhere on the board
+9V: U$2.9V, U$2.9V_1 (9V), U$3.9V, U$3.9V_1 (9V); also elsewhere on the board
GND: NODEMCU.GND@0 (GND), NODEMCU.GND@1 (GND), NODEMCU.GND@2 (GND), NODEMCU.GND@3 (GND), U$1.GND, U$1.GND1 (GND), U$1.GND2 (GND), U$1.GND3 (GND), U$1.GND4 (GND), U$1.GND5 (GND), U$2.GND, U$2.GND1 (GND), U$2.GND2 (GND), U$2.GND3 (GND), U$3.GND, U$3.GND1 (GND), U$3.GND2 (GND), U$3.GND3 (GND); also elsewhere on the board
LED1: NODEMCU.D5, U$1.PD8; also elsewhere on the board
LED2: NODEMCU.D6, U$1.PD9; also elsewhere on the board
LED3: NODEMCU.D7, U$1.PD10; also elsewhere on the board
MISO: NODEMCU.SD0, U$1.PF8, U$2.MISO, U$2.MISO_1 (MISO), U$3.MISO, U$3.MISO_1 (MISO)
MOSI: NODEMCU.SD1, U$1.PF9, U$2.MOSI, U$2.MOSI_1 (MOSI), U$3.MOSI, U$3.MOSI_1 (MOSI)
RX: NODEMCU.RX, U$1.PD2, U$2.RX, U$2.RX_1 (RX), U$3.RX, U$3.RX_1 (RX)
SCK: NODEMCU.CLK, U$1.PF7, U$2.SCK, U$2.SCK_1 (SCK), U$3.SCK, U$3.SCK_1 (SCK)
SCL: NODEMCU.D1, R1.1, U$1.PA8, U$2.SCL, U$2.SCL_1 (SCL), U$3.SCL, U$3.SCL_1 (SCL)
SDA: NODEMCU.D2, R2.1, U$1.PC9, U$2.SDA, U$2.SDA_1 (SDA), U$3.SDA, U$3.SDA_1 (SDA)
TX: NODEMCU.TX, U$1.PC12, U$2.TX, U$2.TX_1 (TX), U$3.TX, U$3.TX_1 (TX)

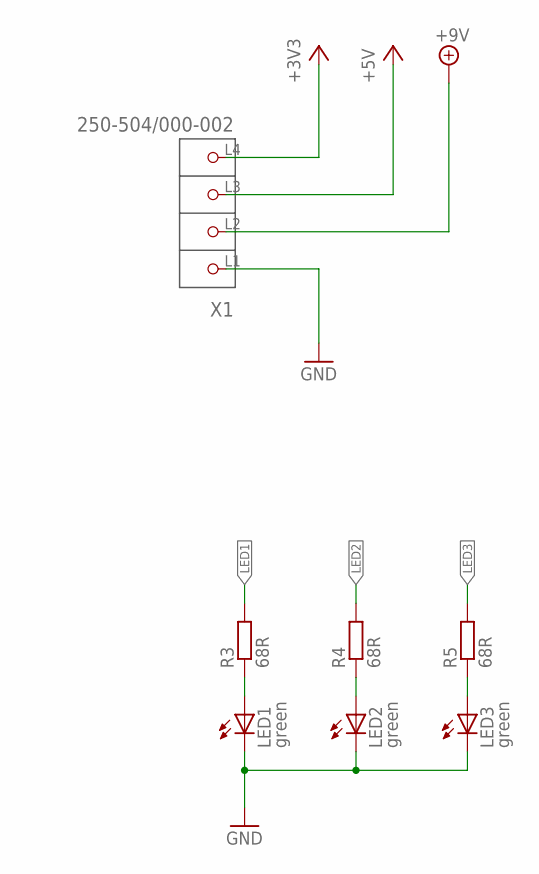
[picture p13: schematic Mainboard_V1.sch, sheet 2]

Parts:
LED1, LED2, LED3: green; CHIP-LED0805
R3, R4, R5: 68R; R0805W
X1: 250-504/000-002; P-250-504

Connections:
+3V3: X1.L4 (P4); also elsewhere on the board
+5V: X1.L3 (P3); also elsewhere on the board
+9V: X1.L2 (P2); also elsewhere on the board
GND: LED1.C, LED2.C, LED3.C, X1.L1 (P1); also elsewhere on the board
LED1: R3.2; also elsewhere on the board
LED2: R4.2; also elsewhere on the board
LED3: R5.2; also elsewhere on the board
unnamed: LED1.A, R3.1
unnamed: LED2.A, R4.1
unnamed: LED3.A, R5.1

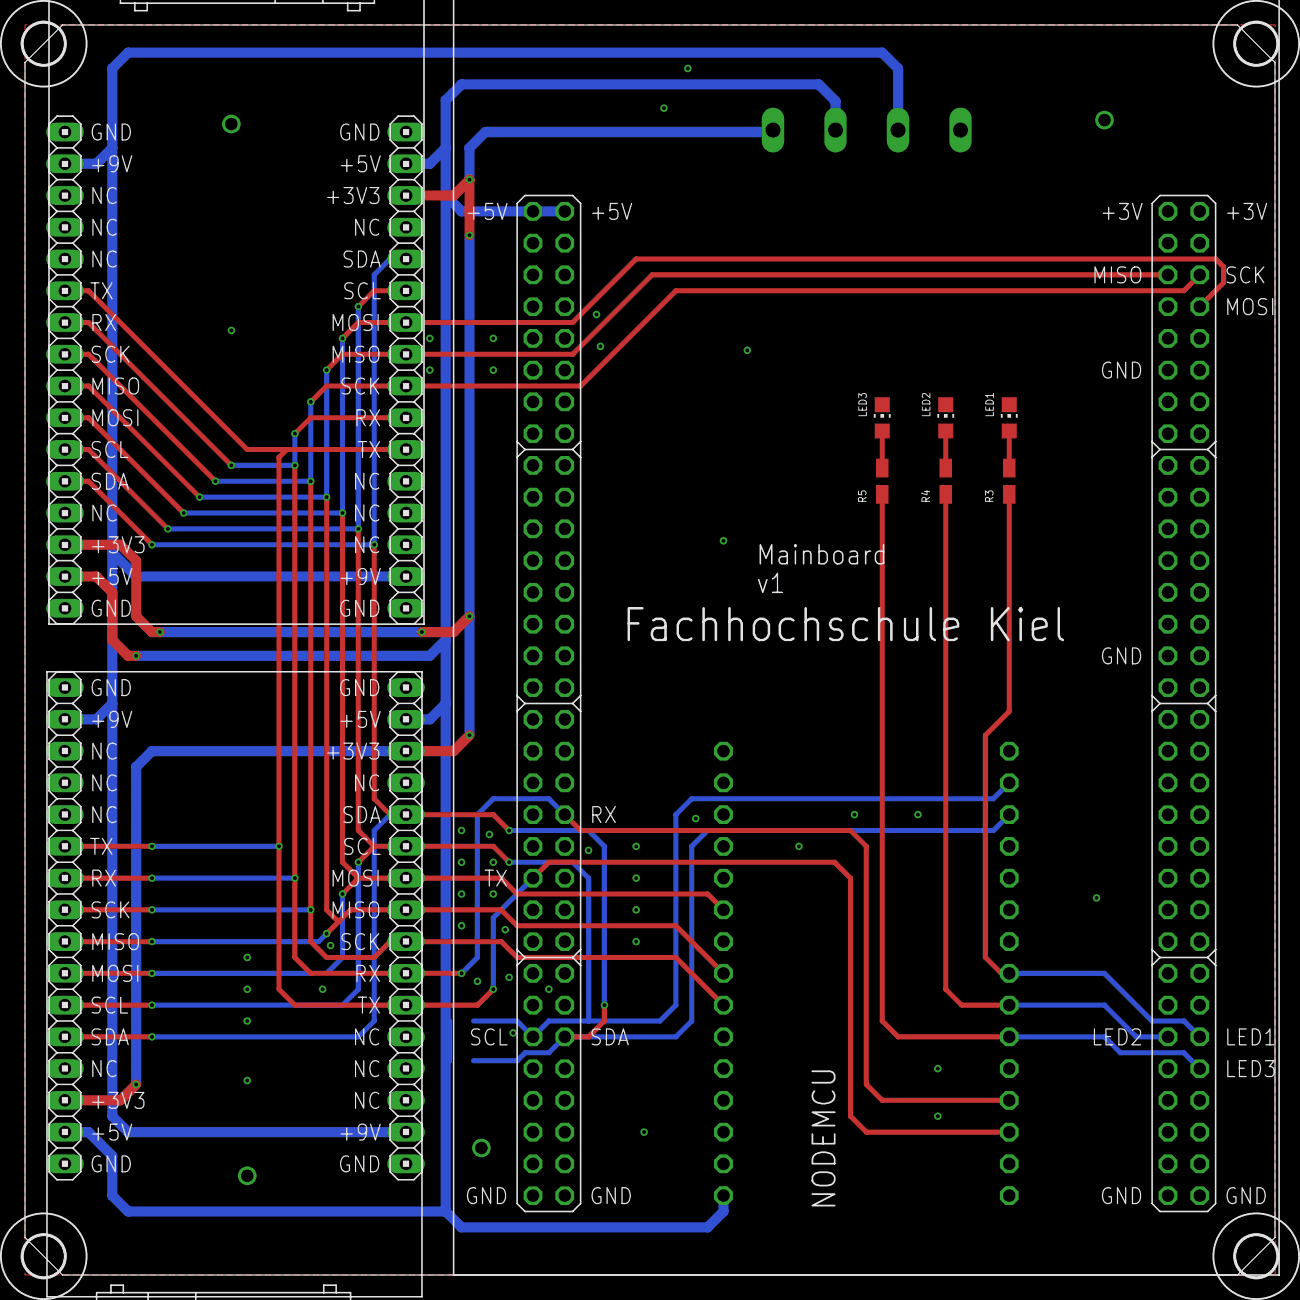
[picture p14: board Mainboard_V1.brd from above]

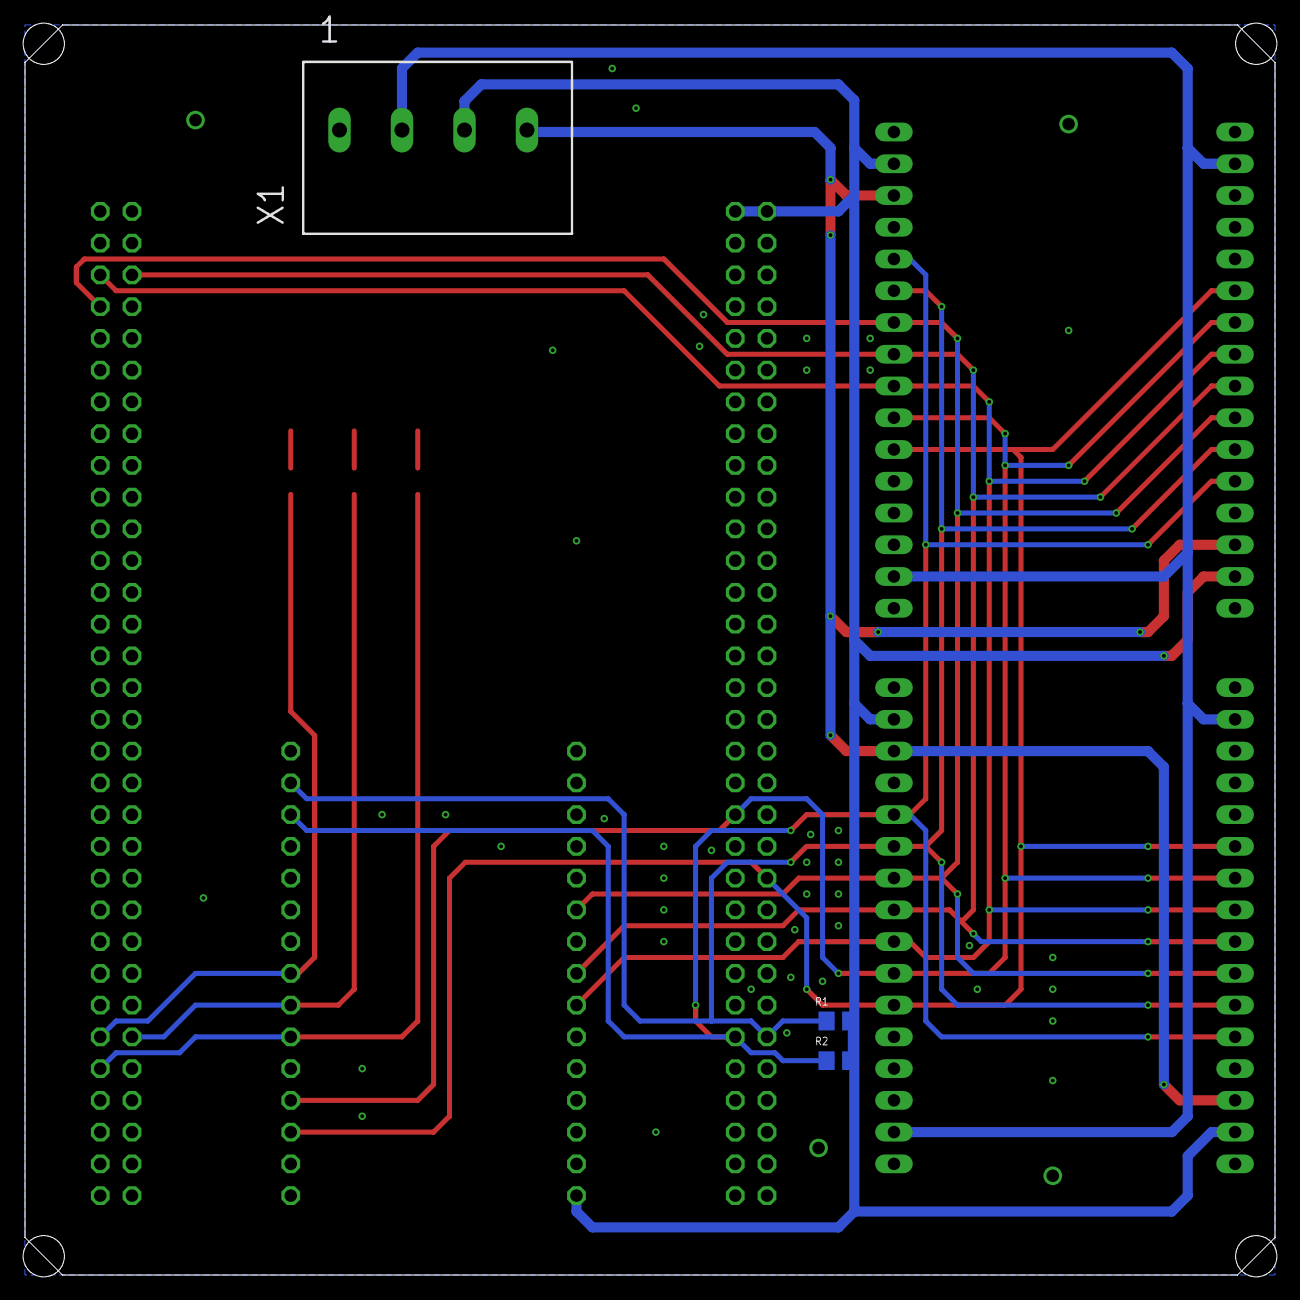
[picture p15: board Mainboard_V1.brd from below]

Board: 2 copper layers, 100.0 x 100.0 mm, 17 parts (3 on the bottom side), 17 nets.

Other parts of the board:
U$4, U$5, U$6, U$7: 3,3

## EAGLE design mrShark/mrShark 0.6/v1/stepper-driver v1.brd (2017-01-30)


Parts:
ADAPTER: ADAPTER_BLANKO_3X5B2; ADAPTER_BLANKO_3X5_B2
C1, C2: 100UF; CAPAE660X610N
C3: 100n; C0805K
IC1: ATMEGA328-AU; TQFP32-08
IC3, IC4: A4988; A4988SHIELD-SMD
ISP: ML10L
LED1: green; CHIP-LED0805
LED2: rot; CHIP-LED0805
R1, R2: 1k8; R0805W
R3: 68R; R0805W
R4: 150R; R0805W
R5: 1k; R0805W
STEP1, STEP2: B5B-XH-A

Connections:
+5V: ADAPTER.5V, ADAPTER.5V_1 (5V), IC1.4 (VCC), IC1.6 (VCC), IC3.VDD, IC4.VDD, ISP.2, R1.2, R2.2, R4.2, R5.1
+9V: ADAPTER.9V, ADAPTER.9V_1 (9V), C1.1, C2.1, IC3.VMOT, IC4.VMOT
AVCC: IC1.18 (AVCC)
GND: ADAPTER.GND, ADAPTER.GND1 (GND), ADAPTER.GND2 (GND), ADAPTER.GND3 (GND), C1.2, C2.2, C3.2, IC1.3 (GND), IC1.5 (GND), IC1.21 (GND), IC3.GND, IC3.GND1 (GND), IC4.GND, IC4.GND1 (GND), ISP.4, ISP.6, ISP.8, ISP.10, LED1.C, LED2.C
MISO: IC1.16 (PB4(MISO)), ISP.9
MOSI: IC1.15 (PB3(MOSI/OC2)), ISP.1
unnamed: C3.1, IC1.20 (AREF)
unnamed: LED1.A, R3.2
unnamed: LED2.A, R4.1
unnamed: IC3.2B, STEP1.5
unnamed: IC3.2A, STEP1.4
unnamed: IC3.1B, STEP1.3
unnamed: IC3.1A, STEP1.2
unnamed: IC4.1A, STEP2.2
unnamed: IC4.1B, STEP2.3
unnamed: IC4.2A, STEP2.4
unnamed: IC4.2B, STEP2.5
RESET: IC1.29 (PC6(/RESET)), ISP.5, R5.2
SCK: IC1.17 (PB5(SCK)), ISP.7, R3.1
SCL: ADAPTER.SCL, ADAPTER.SCL_1 (SCL), IC1.28 (PC5(ADC5/SCL)), R1.1
SDA: ADAPTER.SDA, ADAPTER.SDA_1 (SDA), IC1.27 (PC4(ADC4/SDA)), R2.1
STEP1/DIR: IC1.24 (PC1(ADC1)), IC3.DIR
STEP1/MS1: IC1.25 (PC2(ADC2)), IC3.MS1
STEP1/MS2: IC1.26 (PC3(ADC3)), IC3.MS2
STEP1/MS3: IC1.30 (PD0(RXD)), IC3.MS3
STEP1/RESET: IC3.RESET, IC3.SLEEP
STEP1/STEP: IC1.23 (PC0(ADC0)), IC3.STEP
STEP2/DIR: IC1.32 (PD2(INT0)), IC4.DIR
STEP2/MS1: IC1.1 (PD3(INT1)), IC4.MS1
STEP2/MS2: IC1.2 (PD4(XCK/T0)), IC4.MS2
STEP2/MS3: IC1.9 (PD5(T1)), IC4.MS3
STEP2/RESET: IC4.RESET, IC4.SLEEP
STEP2/STEP: IC1.31 (PD1(TXD)), IC4.STEP

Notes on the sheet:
Fachhochschule Kiel Robotiklabor Grenzstraße 5 24149 Kiel
2x Stepper Driver



Board: 2 copper layers, 30.0 x 50.0 mm, 17 parts (8 on the bottom side), 32 nets.

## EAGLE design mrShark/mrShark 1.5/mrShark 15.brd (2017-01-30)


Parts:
C1, C2: 100n; C0201
C3, C4: 18p; C0201
IC1: ATMEGA168-20MU; MLF32
IC2: PCA9540BDP; TSSOP8
IC3: TIR1000PWR; PW_R-PDSO-G08
IC4: TFBS4711TR1; TFBS4711
LED1: green; CHIPLED_0603
Q1: TXC - 7X-1.8432MBB-T - OSC, 1.8432MHZ; 3.2X2.5
Q9: 14,7456MHZ; TXC_7B_SERIES
R1, R2, R4, R5, R9: 100k; R0201
R6: 87R; R0201
R7, R8: 1k8; R0201
R10: 27R; R0201

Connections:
ADC7: IC1.22 (ADC7); also elsewhere on the board
CLK: IC3.1 (CLK), Q1.3 (FO)
GND: C1.2, C2.2, C3.2, C4.2, IC1.3 (GND), IC1.5 (GND), IC1.21 (AGND), IC2.6 (GND), IC3.4 (GND), IC3.5 (RESET), IC4.6 (GND), LED1.C, Q1.2 (GND), R9.2; also elsewhere on the board
INT0: IC1.32 (PD2(INT0/PCINT18)), R4.2; also elsewhere on the board
INT1: IC1.1 (PD3(INT1/OC2B/PCINT19)), R5.2; also elsewhere on the board
IRDA: IC4.1 (IRDA), R10.2
IR_SD: IC1.2 (PD4(T0/XCK/PCINT20)), IC4.4 (SD), R9.1
LED1: IC1.10 (PD6(AIN0/OC0A/PCINT22)); also elsewhere on the board
LED2: IC1.26 (PC3(ADC3/PCINT11)); also elsewhere on the board
LED3: IC1.9 (PD5(T1/OC0B/PCINT21)); also elsewhere on the board
LED4: IC1.25 (PC2(ADC2/PCINT10)); also elsewhere on the board
LED_B: IC1.13 (PB1(OC1A/PCINT1)); also elsewhere on the board
LED_G: IC1.12 (PB0(ICP1/CLKO/PCINT0)); also elsewhere on the board
LED_R: IC1.11 (PD7(AIN1/PCINT23)); also elsewhere on the board
MISO: IC1.16 (PB4(MISO/PCINT4)); also elsewhere on the board
MOSI: IC1.15 (PB3(MOSI/OC2A/PCINT3)); also elsewhere on the board
unnamed: IC1.14 (PB2(SS/OC1B/PCINT2)), R6.1
unnamed: Q1.1 (OE), R1.2
unnamed: LED1.A, R6.2
unnamed: C2.1, IC1.20 (AREF)
RESET: IC1.29 (PC6(/RESET/PCINT14)), R2.2; also elsewhere on the board
RI2C_EN: IC1.19 (ADC6)
RSCL: IC1.28 (PC5(ADC5/SCL/PCINT13)), IC2.1 (SCL); also elsewhere on the board
RSDA: IC1.27 (PC4(ADC4/SDA/PCINT12)), IC2.2 (SDA); also elsewhere on the board
RXD: IC1.30 (PD0(RXD/PCINT16)), IC3.3 (RXD)
RXIR: IC3.6 (IR_RXD), IC4.3 (RXD)
SCK: IC1.17 (PB5(SCK/PCINT5)); also elsewhere on the board
SCL: IC2.5 (SC0), R8.1; also elsewhere on the board
SDA: IC2.4 (SD0), R7.1; also elsewhere on the board
SRXD: IC1.23 (PC0(ADC0/PCINT8)); also elsewhere on the board
STXD: IC1.24 (PC1(ADC1/PCINT9)); also elsewhere on the board
TXD: IC1.31 (PD1(TXD/PCINT17)), IC3.2 (TXD)
TXIR: IC3.7 (IR_TXD), IC4.2 (TXD)
VCC: C1.1, IC1.4 (VCC), IC1.6 (VCC), IC1.18 (AVCC), IC2.3 (VCC), IC3.8 (VCC), IC4.5 (VCC), Q1.4 (VCC), R1.1, R2.1, R4.1, R5.1, R7.2, R8.2, R10.1; also elsewhere on the board
XTAL1: C3.1, IC1.7 (PB6(XTAL1/TOSC1/PCINT6)), Q9.3 (2)
XTAL2: C4.1, IC1.8 (PB7(XTAL2/TOSC2/PCINT7)), Q9.1

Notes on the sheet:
Fachhochschule Kiel
Grenzstraße 5
24149 Kiel
NorthernStars
Fachbereich IuE
www.northern-stars.de
Controller / IR


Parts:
LED2, LED3, LED4, LED5: ASMT-YTD2-0BB02; PLCC6K
Q2, Q3, Q4, Q5, Q6, Q7, Q8: BC817W; SOT323-BEC
R11, R13: 2k; R0201
R12: 1k; R0201
R14, R15, R16, R17, R18, R23, R24: 100k; R0201
R19, R20, R25, R26: 560R; R0201
R21, R22, R27, R28: 130R; R0201

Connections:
COLOR_B: LED2.1 (BC), LED3.1 (BC), LED4.1 (BC), LED5.1 (BC), Q4.C
COLOR_G: LED2.2 (GC), LED3.2 (GC), LED4.2 (GC), LED5.2 (GC), Q2.C
COLOR_R: LED2.3 (RC), LED3.3 (RC), LED4.3 (RC), LED5.3 (RC), Q3.C
GND: Q2.E, Q3.E, Q4.E, R14.1, R15.1, R16.1, R17.1, R18.1, R23.1, R24.1; also elsewhere on the board
LED1: R17.2, R19.1; also elsewhere on the board
LED2: R18.2, R20.1; also elsewhere on the board
LED3: R23.2, R25.1; also elsewhere on the board
LED4: R24.2, R26.1; also elsewhere on the board
LED_B: R13.2; also elsewhere on the board
LED_G: R11.2; also elsewhere on the board
LED_R: R12.2; also elsewhere on the board
unnamed: LED2.4 (RA), R21.1
unnamed: LED4.4 (RA), R27.1
unnamed: LED4.5 (GA), LED4.6 (BA), Q7.E, R27.2
unnamed: LED3.4 (RA), R22.1
unnamed: LED3.5 (GA), LED3.6 (BA), Q6.E, R22.2
unnamed: Q6.B, R20.2
unnamed: LED5.4 (RA), R28.1
unnamed: LED5.5 (GA), LED5.6 (BA), Q8.E, R28.2
unnamed: Q8.B, R26.2
unnamed: Q7.B, R25.2
unnamed: Q5.B, R19.2
unnamed: LED2.5 (GA), LED2.6 (BA), Q5.E, R21.2
VCC: Q5.C, Q6.C, Q7.C, Q8.C; also elsewhere on the board
X1: Q4.B, R13.1, R16.2
X2: Q3.B, R12.1, R15.2
X3: Q2.B, R11.1, R14.2

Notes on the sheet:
LEDs
Fachhochschule Kiel
Grenzstraße 5
24149 Kiel
NorthernStars
Fachbereich IuE
www.northern-stars.de


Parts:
IC5, IC7: DRV8830DRCT; S-PDSO-N10
IC6: LTC2990IMS#PBF; SOP50P490X110-10N
MOT1, MOT2, MOT3, MOT4: 1,6/0,9
R29, R31: 0.91R; R0603
R30, R32: 0R2; R0603

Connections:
GND: IC5.5 (GND), IC5.7 (A0), IC5.8 (A1), IC5.PP (EP), IC5.PP@1 (EP), IC5.PP@2 (EP), IC6.5 (GND), IC6.8 (ADR0), IC6.9 (ADR1), IC7.5 (GND), IC7.8 (A1), IC7.PP (EP), IC7.PP@1 (EP), IC7.PP@2 (EP), R29.1, R31.1; also elsewhere on the board
unnamed: IC5.1 (OUT2), MOT1.1
unnamed: IC5.2 (ISENSE), R29.2
unnamed: IC7.1 (OUT2), MOT3.1
unnamed: IC7.2 (ISENSE), R31.2
SCL: IC5.10 (SCL), IC6.7 (SCL), IC7.10 (SCL); also elsewhere on the board
SDA: IC5.9 (SDA), IC6.6 (SDA), IC7.9 (SDA); also elsewhere on the board
SENS_MOTL1: IC5.3 (OUT1), IC6.1 (V1), R30.1
SENS_MOTL2: IC6.2 (V2), MOT2.1, R30.2
SENS_MOTR1: IC6.3 (V3), IC7.3 (OUT1), R32.1
SENS_MOTR2: IC6.4 (V4), MOT4.1, R32.2
VCC: IC5.4 (VCC), IC6.10 (VCC), IC7.4 (VCC), IC7.7 (A0); also elsewhere on the board

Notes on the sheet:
MOTORS
Fachhochschule Kiel
Grenzstraße 5
24149 Kiel
NorthernStars
Fachbereich IuE
www.northern-stars.de


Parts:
BAT1+1, BAT1-1, BAT2+1, BAT2-1: 1,6/0,9
C5: 10µ; C0603K
CON_PROG: DF12(5.0)-20DP-0.5V; DF12-20DP
D1, D2: PMEG2010EA; SOD323-R
H1, H2, H3, H4: MOUNT-HOLE1,5; 1,5
IC8: LTC2990IMS#PBF; SOP50P490X110-10N
LED6: red; CHIPLED_0603
R33: 200R; R0201
R34, R35: 1k8; R0201
SWITCH_PWR: AYZ0202AGRLC; AYZ0202AGLRC

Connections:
ADC7: CON_PROG.17; also elsewhere on the board
BAT1: BAT1+1.1, SWITCH_PWR.2
BAT1+: D1.A, IC8.1 (V1), SWITCH_PWR.1 (O)
BAT2: BAT2+1.1, SWITCH_PWR.5 (P1)
BAT2+: D2.A, IC8.2 (V2), SWITCH_PWR.4 (O1)
GND: BAT1-1.1, BAT2-1.1, C5.2, CON_PROG.2, CON_PROG.5, CON_PROG.16, IC8.5 (GND), IC8.9 (ADR1), LED6.C; also elsewhere on the board
I2C_ADC0: CON_PROG.13, IC8.3 (V3)
I2C_ADC1: CON_PROG.12, IC8.4 (V4)
INT0: CON_PROG.4; also elsewhere on the board
INT1: CON_PROG.3; also elsewhere on the board
MISO: CON_PROG.19; also elsewhere on the board
MOSI: CON_PROG.20; also elsewhere on the board
unnamed: LED6.A, R33.1
P_BAT1+: CON_PROG.14, SWITCH_PWR.3 (S)
P_BAT2+: CON_PROG.15, SWITCH_PWR.6 (S1)
RESET: CON_PROG.7; also elsewhere on the board
RSCL: CON_PROG.8, R34.1; also elsewhere on the board
RSDA: CON_PROG.9, R35.1; also elsewhere on the board
SCK: CON_PROG.18; also elsewhere on the board
SCL: IC8.7 (SCL); also elsewhere on the board
SDA: IC8.6 (SDA); also elsewhere on the board
SRXD: CON_PROG.11; also elsewhere on the board
STXD: CON_PROG.10; also elsewhere on the board
VCC: C5.1, CON_PROG.1, D1.C, D2.C, IC8.8 (ADR0), IC8.10 (VCC), R33.2, R34.2, R35.2; also elsewhere on the board

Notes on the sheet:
CONNECTORS
Fachhochschule Kiel
Grenzstraße 5
24149 Kiel
NorthernStars
Fachbereich IuE
www.northern-stars.de
MCCA000517



Board: 2 copper layers, 26.0 x 31.0 mm, 78 parts (37 on the bottom side), 70 nets.

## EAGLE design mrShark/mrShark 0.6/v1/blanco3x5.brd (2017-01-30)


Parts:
ISP: ML10L
LED1: green; CHIP-LED0805
LED2: rot; CHIP-LED0805
R3: 68R; R0805W
R4: 150R; R0805W
U$1: ADAPTER_BLANKO_3X5B2; ADAPTER_BLANKO_3X5_B2

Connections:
+5V: ISP.2, R4.2, U$1.5V, U$1.5V_1 (5V)
GND: ISP.4, ISP.6, ISP.8, ISP.10, LED1.C, LED2.C, U$1.GND, U$1.GND1 (GND), U$1.GND2 (GND), U$1.GND3 (GND)
MISO: ISP.9
MOSI: ISP.1
unnamed: LED1.A, R3.2
unnamed: LED2.A, R4.1
RESET: ISP.5
SCK: ISP.7, R3.1

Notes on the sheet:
Fachhochschule Kiel Robotiklabor Grenzstraße 5 24149 Kiel


Board: 2 copper layers, 30.0 x 50.0 mm, 6 parts (0 on the bottom side), 5 nets.

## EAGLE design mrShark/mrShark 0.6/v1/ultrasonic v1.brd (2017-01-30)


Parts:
C1: 100n; C0805
IC1: ATtiny48; TQFP32-08
ISP: ML10L
LED1: green; CHIP-LED0805
LED2, LED3: rot; CHIP-LED0805
R1: 1k; R0805W
R2, R5: 1k8; R0805W
R3: 68R; R0805W
R4, R6: 150R; R0805W
SERVO1, SERVO2, SERVO3, SERVO4, SERVO5, SERVO6: PINHD-1X3; 1X03
U$1: ADAPTER_BLANKO_3X5B2; ADAPTER_BLANKO_3X5_B2
US1, US2, US3, US4, US5, US6: PINHD-1X4; 1X04

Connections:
+5V: IC1.4 (VCC), IC1.6 (VCC), ISP.2, R1.1, R2.1, R4.2, R5.1, SERVO1.2, SERVO2.2, SERVO3.2, SERVO4.2, SERVO5.2, SERVO6.2, U$1.5V, U$1.5V_1 (5V), US1.1, US2.1, US3.1, US4.1, US5.1, US6.1
GND: C1.2, IC1.3 (GND), IC1.5 (GND), IC1.21 (AGND), ISP.4, ISP.6, ISP.8, ISP.10, LED1.C, LED2.C, LED3.C, SERVO1.3, SERVO2.3, SERVO3.3, SERVO4.3, SERVO5.3, SERVO6.3, U$1.GND, U$1.GND1 (GND), U$1.GND2 (GND), U$1.GND3 (GND), US1.4, US2.4, US3.4, US4.4, US5.4, US6.4
MISO: IC1.16 (PB4(MISO)), ISP.9
MOSI: IC1.15 (PB3(MOSI/OC2)), ISP.1
unnamed: IC1.8 (PB7(XTAL2/TOSC2)), R6.2
unnamed: LED3.A, R6.1
unnamed: LED1.A, R3.2
unnamed: LED2.A, R4.1
unnamed: C1.1, IC1.20 (AREF)
RESET: IC1.29 (PC6(/RESET)), ISP.5, R1.2
SCK: IC1.17 (PB5(SCK)), ISP.7, R3.1
SCL: IC1.28 (PC5(ADC5/SCL)), R5.2, U$1.SCL, U$1.SCL_1 (SCL)
SDA: IC1.27 (PC4(ADC4/SDA)), R2.2, U$1.SDA, U$1.SDA_1 (SDA)
SERVO1: IC1.30 (PD0(RXD)), SERVO1.1
SERVO2: IC1.31 (PD1(TXD)), SERVO2.1
SERVO3: IC1.32 (PD2(INT0)), SERVO3.1
SERVO4: IC1.1 (PD3(INT1)), SERVO4.1
SERVO5: IC1.2 (PD4(T0/XCK)), SERVO5.1
SERVO6: IC1.9 (PD5(T1)), SERVO6.1
US1_ECHO: IC1.19 (ADC6), US1.3
US1_TRIG: IC1.10 (PD6(AIN0)), US1.2
US2_ECHO: IC1.22 (ADC7), US2.3
US2_TRIG: IC1.7 (PB6(XTAL1/TOSC1)), US2.2
US3_ECHO: IC1.23 (PC0(ADC0)), US3.3
US3_TRIG: IC1.11 (PD7(AIN1)), US3.2
US4_ECHO: IC1.24 (PC1(ADC1)), US4.3
US4_TRIG: IC1.12 (PB0(ICP1)), US4.2
US5_ECHO: IC1.25 (PC2(ADC2)), US5.3
US5_TRIG: IC1.13 (PB1(OC1A)), US5.2
US6_ECHO: IC1.26 (PC3(ADC3)), US6.3
US6_TRIG: IC1.14 (PB2(SS/OC1B)), US6.2

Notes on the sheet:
Fachhochschule Kiel Robotik Labor Grenzstraße 5 24149 Kiel
6x US-Sensor & Servo


Board: 2 copper layers, 30.0 x 50.0 mm, 25 parts (1 on the bottom side), 31 nets.

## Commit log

2014-11-25 Restructured mrShark subdirectory.
    [mrShark 01.a.brd, mrShark 01.a.sch, mrShark 01.a_nutzen.brd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]
2014-11-25 Updated LiPo-Charger MultiBoard schematic and board.
    [multiboard.brd, multiboard.sch]
2014-11-26 Added Bot dimension to LiPo-Charger MultiBoard layout.
    [multiboard.brd]
2014-11-26 Renamed Mulitboard charger board. Added MultiBoard Supply board.
    [charger.brd, charger.sch, supply.brd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]
2014-11-26 Updated schematics and board. Added LibreOffice calculation for part lists.
    [Parts-Calculation.ods, charger.brd, charger.sch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]
2014-11-26 Updated information for LiPo-Charger MulitBoard
    [charger.brd, supply.brd]
2014-11-26 Fixed errors in LiPo-Charger-Station
    [lipo-charger-station.brd, lipo-charger-station.sch]
2014-11-26 Updated IR-Splitter
    [ir-splitter.brd, ir-splitter.sch]
2014-11-26 Changed size of IR_Transmitter to fit dirtypcbs.com 50x50mm size.
    [irda-usb-transmitter-V3.brd, irda-usb-transmitter-V3.sch]
2014-11-26 Added a jumper to switch between USB power and extranl power for IR-Transmitter. Updated README.md
    [irda-usb-transmitter-V3.brd, irda-usb-transmitter-V3.sch]
2014-11-30 Updated mrShark board layout to avoid electrict short circuits while charging with wrong board orientantion.
    [mrShark 12.brd, mrShark 12.sch]
2014-11-30 Added mrShark board image
2015-01-06 Fixed IR-Transmitter board
    [irda-usb-transmitter-V3.brd]
2015-01-06 Updated LiPo-Charger Multiboard layout and parts calculation
    [Parts-Calculation.ods, charger.brd]
2015-01-06 Updated mrShark v. 1.1 layout and schematic
    [mrShark 11.brd]
2015-01-06 Updated mrShark v1.2 layout
    [mrShark 12.brd]
2015-01-06 Updated mrShark Debugger layout
    [mrShark Debugger.brd]
2015-01-16 Updated IR Splitter schematics and layout to avoid damage of IR leds
    [ir-splitter.brd]
2015-01-22 Updated IR-Splitter to Version 1.0.0
    [ir-splitter.brd, ir-splitter.sch, irda-usb-transmitter-V3.brd]
2015-01-22 Added optional resistors R2 & R3 to schematics and layout.
    [irda-usb-transmitter-V3.brd, irda-usb-transmitter-V3.sch]
2015-04-27 Updated mr Shark Layout and added LED-Marker
    [mrShark 01.a_nutzen.brd, mrShark 13.brd, mrShark 13.sch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]
2015-05-06 Updated LED-marker to version 0.0.1
    [mrShark LED-Marker.brd, mrShark LED-Marker.sch]
2015-05-06 Updated LED-marker
    [mrShark LED-Marker.brd, mrShark LED-Marker.sch]
2015-05-06 Added switchable position lights
    [mrShark LED-Marker.brd, mrShark LED-Marker.sch]
2015-05-27 Updated revision number in board layout.
    [mrShark LED-Marker.brd]
2015-08-04 Updated mrShark 1.2 & 1.3 Updated mrShark Adapter Updated mrShark LED-Marker to version 0.0.3
    [mrShark 12.brd, mrShark 12.sch, mrShark 13.brd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]
2016-06-01 Updated LED Marker to version 1.0 Fixed a bug with wrong placed led and updated connection header layout.
    [mrShark 13.brd, mrShark LED-Marker.brd, mrShark LED-Marker.sch]
2016-06-01 Updated mrShark to Version 1.4 Updated connector layout and fixed some corresponding layout errors.
    [mrShark 14.brd, mrShark 14.sch]
2016-06-01 Updated to version 0.0.1 Updated connector layout
    [charger.brd, charger.sch]
2016-06-01 Updated to new connector layout.
    [mrShark Adapter.brd, mrShark Adapter.sch]
2016-06-01 Updated layouts and added parts lists
    [charger.csv, ir-splitter.brd, ir-splitter.csv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]
2016-07-12 Fixed error in board layout
    [mrShark 15.brd, mrShark 15.sch]
2016-12-20 Added second version of mrShark Adapter that should be solderable by hand.
    [mrShark Adapter.brd, mrShark Adapter.csv, mrShark Adapter.sch]
2017-01-30 Updated Board layouts an schematics
    [Mainboard_V1.brd, Mainboard_V1.sch, blanco3x5.brd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]
2017-01-30 Updated adapter to hirose mini usb connector
    [mrShark Adapter.brd, mrShark Adapter.sch]
2017-02-16 Fixed layout errors. Layout is now tested.
    [irda-usb-transmitter-V3.brd, irda-usb-transmitter-V3.sch]
2018-05-22 Updated README of LED Marker and Lists
2018-05-22 Updated layout and added gerber files.
    [mrShark LED-Marker.brd, mrShark LED-Marker.csv]
2018-05-22 Fixed wrong files
    [Adapter-Board.brd, Adapter-Board.sch, Controler-Board.brd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]
